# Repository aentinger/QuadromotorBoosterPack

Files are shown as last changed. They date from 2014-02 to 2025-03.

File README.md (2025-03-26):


💾 Quadromotor BoosterPack
==========================



# 📸 Image

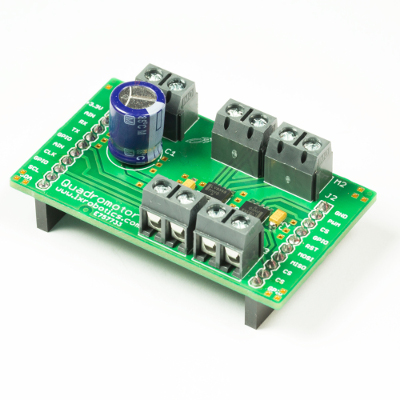
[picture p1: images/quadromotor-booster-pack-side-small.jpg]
LXRobotics P7 Quadromotor BoosterPack


# 📂 Description

The Quadromotor BoosterPack in combination with a MSP430 Launchpad facilitates the control of a 1, 2 or 4 DC motors, or alternatively  of 2 stepper motors. Additionally, outputs of the motor drivers can be connected in parallel. Therefor, two motors with an maximum output current of 2 A can be controlled, or one motor with an maximum output current of 4 A. For a quick and easy start a sample Code Composer Studio project (written in programming language C) is available.

**Features**

* Control of 1, 2 or 4 DC motors OR 
* Control of 2 stepper motors
* Speed and rotational direction adjustable
* Supply voltage range: 4 V to 16 V
* Output current per motor for 4/2/1 motors: 1 A / 2 A / 4 A
* To be used with MSP430 Launchpad
* Sample projects available for Code Composer Studio

# 🎥 [Video](images/quadromotor_booster_pack_demo.mp4)

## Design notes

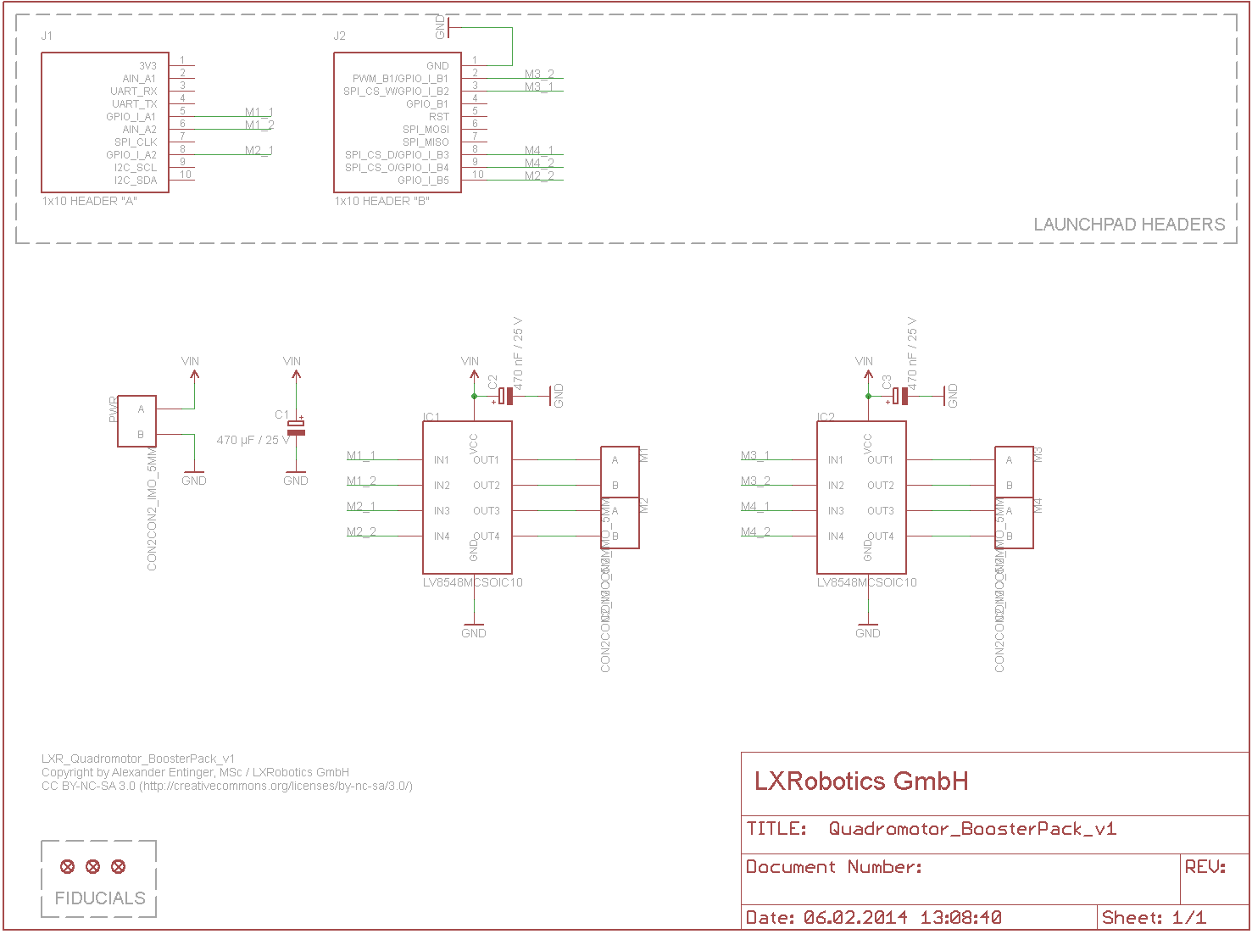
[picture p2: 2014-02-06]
hardware/lxr_quadromotor_boosterpack_v1.png

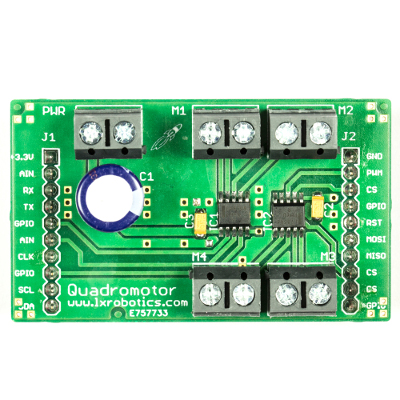
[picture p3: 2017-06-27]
images/quadromotor-booster-pack-top-small.jpg

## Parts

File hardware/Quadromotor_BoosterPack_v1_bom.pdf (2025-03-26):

Menge | Schaltplan | Bezeichnung | Farnell/Conrad Bestell Nummer | Preis (1 Stück) | Gesamtpreis | Wird bestückt | Footprint | Säckchen
2 | IC1, IC2 | LV8548MC-Motortreiber 2 CH | 2217011 | € 2,78 | € 5,56 | x
5 | PWR, M1, M2, M3, M4 | CON2, 5 mm, schwarz | 9632972 | € 0,42 | € 2,10 | | | S1
1 | C1 | 470 µF, 25 V, Elko, Radial | 1848502 | € 0,37 | € 0,37 | | | S1
2 | C2, C3 | KEMET Bauform A, 25 V, 470 nF, Tantal Ko | 1457425 | € 0,28 | € 0,56 | x
2 | J1, J2 | Pin-Header, 10-Polig, 2.54 mm | 1593464 | € 1,52 | € 3,04 | | | S1
Summe | € | 11,63

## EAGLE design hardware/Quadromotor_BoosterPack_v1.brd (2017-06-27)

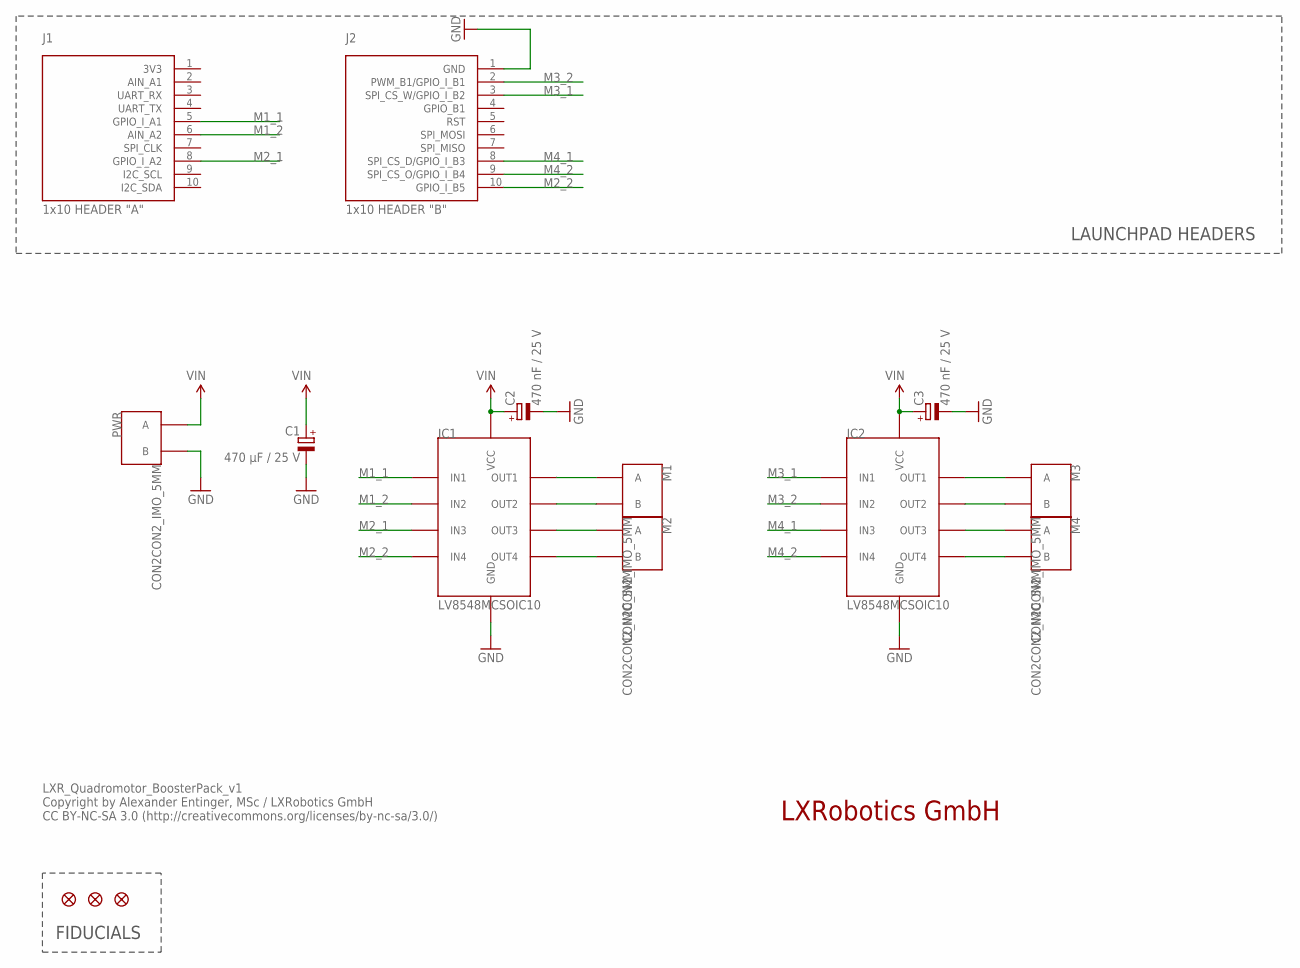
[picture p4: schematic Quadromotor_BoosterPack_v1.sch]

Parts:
C1: 470 µF / 25 V; E5-10,5
C2, C3: 470 nF / 25 V; KEMET_A
FID1, FID2, FID3: FIDUCIAL; FIDUCIAL_L10
IC1, IC2: LV8548MCSOIC10; SOIC10
J1: 1x10 HEADER "A"; 1X10
J2: 1x10 HEADER "B"; 1X10
M1, M2, M3, M4: CON2CON2_IMO_5MM; CON2_IMO
PWR: CON2CON2_IMO_5MM; CON2_IMO

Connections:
GND: C1.-, C2.CATHODE (-), C3.CATHODE (-), IC1.6 (GND), IC2.6 (GND), J2.1 (GND), PWR.P$2 (B)
M1_1: IC1.2 (IN1), J1.5 (GPIO_I_A1)
M1_2: IC1.3 (IN2), J1.6 (AIN_A2)
M2_1: IC1.4 (IN3), J1.8 (GPIO_I_A2)
M2_2: IC1.5 (IN4), J2.10 (GPIO_I_B5)
M3_1: IC2.2 (IN1), J2.3 (SPI_CS_W/GPIO_I_B2)
M3_2: IC2.3 (IN2), J2.2 (PWM_B1/GPIO_I_B1)
M4_1: IC2.4 (IN3), J2.8 (SPI_CS_D/GPIO_I_B3)
M4_2: IC2.5 (IN4), J2.9 (SPI_CS_O/GPIO_I_B4)
unnamed: IC1.10 (OUT1), M1.P$1 (A)
unnamed: IC1.9 (OUT2), M1.P$2 (B)
unnamed: IC1.8 (OUT3), M2.P$1 (A)
unnamed: IC1.7 (OUT4), M2.P$2 (B)
unnamed: IC2.10 (OUT1), M3.P$1 (A)
unnamed: IC2.9 (OUT2), M3.P$2 (B)
unnamed: IC2.8 (OUT3), M4.P$1 (A)
unnamed: IC2.7 (OUT4), M4.P$2 (B)
VIN: C1.+, C2.ANODE (+), C3.ANODE (+), IC1.1 (VCC), IC2.1 (VCC), PWR.P$1 (A)

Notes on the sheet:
LAUNCHPAD HEADERS
FIDUCIALS
LXRobotics GmbH
LXR_Quadromotor_BoosterPack_v1 Copyright by Alexander Entinger, MSc / LXRobotics GmbH CC BY-NC-SA 3.0 (http://creativecommons.org/licenses/by-nc-sa/3.0/)

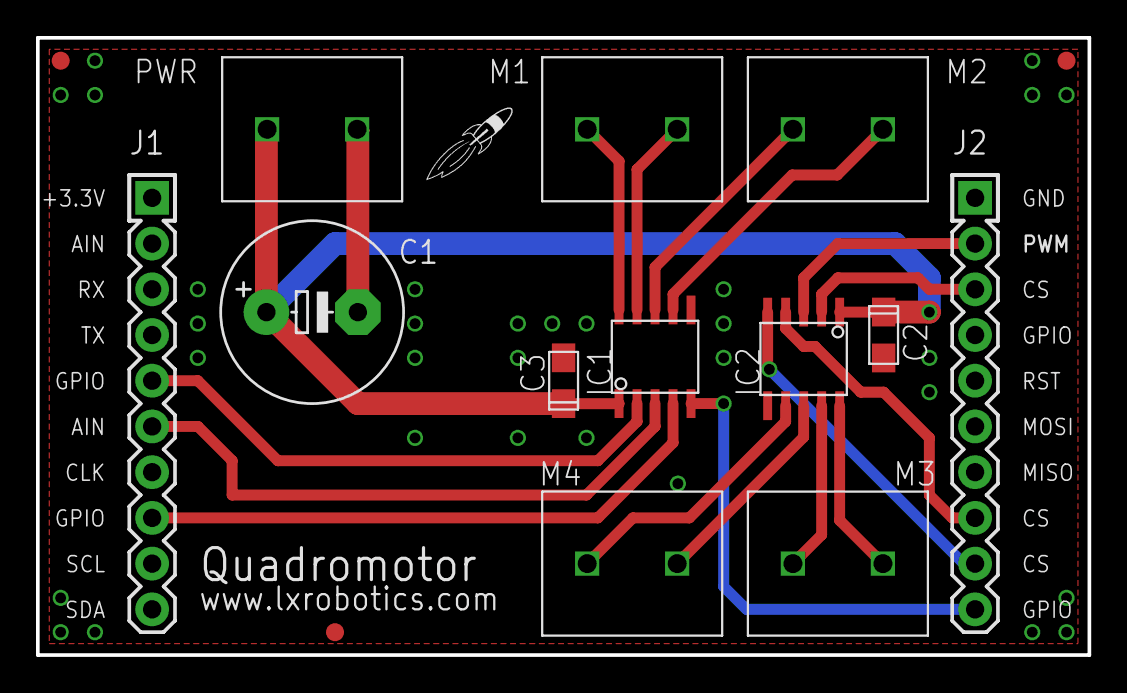
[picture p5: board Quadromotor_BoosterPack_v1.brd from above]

Board: 2 copper layers, 58.4 x 34.3 mm, 16 parts (0 on the bottom side), 18 nets.

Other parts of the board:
U$1: LOGO-ROCKET

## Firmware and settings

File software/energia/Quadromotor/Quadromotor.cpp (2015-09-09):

/**
 * @author Alexander Entinger, MSc
 * @brief energia library file for the LXRobotics Quadromotor Booster Pack ( https://www.lxrobotics.com/produkte/booster-packs/quadromotor-boosterpack )
 * @file Quadromotor.h
 * @license CC BY-NC-SA 3.0 ( http://creativecommons.org/licenses/by-nc-sa/3.0/ )
 */
 
/* INCLUDES */

#include "Quadromotor.h"

/* FUNCTIONS */

/* C */

#include <msp430.h>

/* DEFINES */
#define M1_1_DIR		(P1DIR)
#define M1_2_DIR		(P1DIR)
#define M1_1_OUT		(P1OUT)
#define M1_2_OUT		(P1OUT)
#define M1_1			(1<<3)
#define M1_2			(1<<4)

#define M2_1_DIR		(P2DIR)
#define M2_2_DIR		(P2DIR)
#define M2_1_OUT		(P2OUT)
#define M2_2_OUT		(P2OUT)
#define M2_1			(1<<0)
#define M2_2			(1<<3)

#define M3_1_DIR		(P2DIR)
#define M3_2_DIR		(P2DIR)
#define M3_1_OUT		(P2OUT)
#define M3_2_OUT		(P2OUT)
#define M3_1			(1<<7)
#define M3_2			(1<<6)

#define M4_1_DIR		(P2DIR)
#define M4_2_DIR		(P2DIR)
#define M4_1_OUT		(P2OUT)
#define M4_2_OUT		(P2OUT)
#define M4_1			(1<<5)
#define M4_2			(1<<4)

/* MACROS */
#define M1_1_HIGH		M1_1_OUT |= M1_1
#define M1_1_LOW		M1_1_OUT &= ~M1_1
#define M1_2_HIGH		M1_2_OUT |= M1_2
#define M1_2_LOW		M1_2_OUT &= ~M1_2

#define M2_1_HIGH		M2_1_OUT |= M2_1
#define M2_1_LOW		M2_1_OUT &= ~M2_1
#define M2_2_HIGH		M2_2_OUT |= M2_2
#define M2_2_LOW		M2_2_OUT &= ~M2_2

#define M3_1_HIGH		M3_1_OUT |= M3_1
#define M3_1_LOW		M3_1_OUT &= ~M3_1
#define M3_2_HIGH		M3_2_OUT |= M3_2
#define M3_2_LOW		M3_2_OUT &= ~M3_2

#define M4_1_HIGH		M4_1_OUT |= M4_1
#define M4_1_LOW		M4_1_OUT &= ~M4_1
#define M4_2_HIGH		M4_2_OUT |= M4_2
#define M4_2_LOW		M4_2_OUT &= ~M4_2

/* DATA TYPES */

typedef struct {
	uint16_t speed;
	E_DIRECTION dir;
} s_motor_params;

/* GLOBAL VARIABLES */

static volatile s_motor_params m_motor_1 = {0, FWD};
static volatile s_motor_params m_motor_2 = {0, FWD};
static volatile s_motor_params m_motor_3 = {0, FWD};
static volatile s_motor_params m_motor_4 = {0, FWD};

/* GLOBAL FUNCTIONS */

/**
 * @brief initializes the booster pack
 */
void init_quadromotor_booster_pack()  {
	// set all gpios to outputs and low
	M1_1_DIR |= M1_1;	M1_1_LOW;
	M1_2_DIR |= M1_2;	M1_2_LOW;
	M2_1_DIR |= M2_1;	M2_1_LOW;
	M2_2_DIR |= M2_2;	M2_2_LOW;
	M3_1_DIR |= M3_1;	M3_1_LOW;
	M3_2_DIR |= M3_2;	M3_2_LOW;
	M4_1_DIR |= M4_1;	M4_1_LOW;
	M4_2_DIR |= M4_2;	M4_2_LOW;

	// disable all secondary port functions
	P1SEL = 0x00; P1SEL2 = 0x00;
	P2SEL = 0x00; P2SEL2 = 0x00;

	TA0CTL |= TASSEL_2;	// select SMCLK as clock source, thats 16 MHz, divider = 8, 1 timerstep = 500 ns
	TA0CTL |= 0xC0;
	TA0CTL |= TACLR;		// clear the timer

	TA0CCR0 = 2016;		// equals 1 ms
	TA0CCTL0 &= CCIFG;
	TA0CCTL0 |= CCIE;		// enable capture compare interrupt

	TA0CTL &= ~TAIFG;	// clear the inerrupt flag
	TA0CTL |= TAIE;		// enable the interrupt
	TA0CTL |= MC_1;		// timer counts up to TACCR0

	TA0CCR1 = 0x0000;
	TA0CCTL1 &= CCIFG;
	TA0CCTL1 |= CCIE;		// enable capture compare interrupt

	TA0CCR2 = 0x0000;
	TA0CCTL2 &= CCIFG;
	TA0CCTL2 |= CCIE;		// enable capture compare interrupt

	TA1CTL |= TASSEL_2;	// select SMCLK as clock source, thats 16 MHz, divider = 8, 1 timerstep = 500 ns
	TA1CTL |= 0xC0;
	TA1CTL |= TACLR;		// clear the timer

	TA1CCR0 = 2016;		// equals 1 ms
	TA1CCTL0 &= CCIFG;
	TA1CCTL0 |= CCIE;		// enable capture compare interrupt

	TA1CTL &= ~TAIFG;	// clear the inerrupt flag
	TA1CTL |= TAIE;		// enable the interrupt
	TA1CTL |= MC_1;		// timer counts up to TACCR0

	TA1CCR1 = 0x0000;
	TA1CCTL1 &= CCIFG;
	TA1CCTL1 |= CCIE;		// enable capture compare interrupt
	TA1CCR2 = 0x0000;
	TA1CCTL2 &= CCIFG;
	TA1CCTL2 |= CCIE;		// enable capture compare interrupt
}

/**
 * @brief set speed for motor 1
 * @param speed 0 means no speak and 1000 means full speed
 */
void motor_1_set_speed(uint16_t const speed) {
	noInterrupts();
	if(speed <= MAX_SPEED) {
		m_motor_1.speed = (speed<<1); // multiply with 2
	}
	interrupts();
}

/**
 * @brief set direction for motor 1
 */
void motor_1_set_direction(E_DIRECTION const dir) {
	noInterrupts();
	m_motor_1.dir = dir;
	interrupts();
}

/**
 * @brief set speed for motor 2
 * @param speed 0 means no speak and 1000 means full speed
 */
void motor_2_set_speed(uint16_t const speed) {
	noInterrupts();
	if(speed <= MAX_SPEED) {
		m_motor_2.speed = (speed<<1); // multiply with 2
	}
	interrupts();
}

/**
 * @brief set direction for motor 2
 */
void motor_2_set_direction(E_DIRECTION const dir) {
	noInterrupts();
	m_motor_2.dir = dir;
	interrupts();
}

/**
 * @brief set speed for motor 3
 * @param speed 0 means no speak and 1000 means full speed
 */
void motor_3_set_speed(uint16_t const speed) {
	noInterrupts();
	if(speed <= MAX_SPEED) {
		m_motor_3.speed = (speed<<1); // multiply with 2
	}
	interrupts();
}

/**
 * @brief set direction for motor 3
 */
void motor_3_set_direction(E_DIRECTION const dir) {
	noInterrupts();
	m_motor_3.dir = dir;
	interrupts();
}

/**
 * @brief set speed for motor 4
 * @param speed 0 means no speak and 1000 means full speed
 */
void motor_4_set_speed(uint16_t const speed) {
	noInterrupts();
	if(speed <= MAX_SPEED) {
		m_motor_4.speed = (speed<<1); // multiply with 2
	}
	interrupts();
}

/**
 * @brief set direction for motor 4
 */
void motor_4_set_direction(E_DIRECTION const dir) {
	noInterrupts();
	m_motor_4.dir = dir;
	interrupts();
}

/**
 * @brief Timer A0 Interrupt Service Routine for CCR0
 */
#pragma vector=TIMER0_A0_VECTOR
__interrupt void TIMER0_A0_ISR(void) {
	// update the capture compare registers
	TA0CCR1 = m_motor_1.speed;
	TA0CCR2 = m_motor_2.speed;
	// set the pins
	if(m_motor_1.speed > 0) {
		if(m_motor_1.dir == FWD) {
			M1_1_HIGH; M1_2_LOW;
		} else if(m_motor_1.dir == BWD) {
			M1_1_LOW; M1_2_HIGH;
		}
	} else {
		M1_1_LOW; M1_2_LOW;
	}
	if(m_motor_2.speed > 0) {
		if(m_motor_2.dir == FWD) {
			M2_1_HIGH; M2_2_LOW;
		} else if(m_motor_2.dir == BWD) {
			M2_1_LOW; M2_2_HIGH;
		}
	} else {
		M2_1_LOW; M2_2_LOW;
	}
}

/**
 * @brief Timer A0 Interrupt Service Routine for all the other interrupts
 */
#pragma vector=TIMER0_A1_VECTOR
__interrupt void TIMER0_A1_ISR(void) {

	switch (TA0IV) {
	case 0: break; // no interrupt
	case 2: {
		M1_1_LOW; M1_2_LOW;
	}
		break;
	case 4: {
		M2_1_LOW; M2_2_LOW;
	}
		break;
	case 6:	break; // reserved
	case 8:	break; // reserved
	case 10: break; // overflow
	default: break;
	}
}

/**
 * @brief Timer A1 Interrupt Service Routine for CCR0
 */
#pragma vector=TIMER1_A0_VECTOR
__interrupt void TIMER1_A0_ISR(void) {
	// update the capture compare registers
	TA1CCR1 = m_motor_3.speed;
	TA1CCR2 = m_motor_4.speed;
	// set the pins
	if(m_motor_3.speed > 0) {
		if(m_motor_3.dir == FWD) {
			M3_1_HIGH; M3_2_LOW;
		} else if(m_motor_3.dir == BWD) {
			M3_1_LOW; M3_2_HIGH;
		}
	} else {
		M3_1_LOW; M3_2_LOW;
	}
	if(m_motor_4.speed > 0) {
		if(m_motor_4.dir == FWD) {
			M4_1_HIGH; M4_2_LOW;
		} else if(m_motor_4.dir == BWD) {
			M4_1_LOW; M4_2_HIGH;
		}
	} else {
		M4_1_LOW; M4_2_LOW;
	}
}
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

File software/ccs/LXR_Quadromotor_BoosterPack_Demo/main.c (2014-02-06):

/**
 * @author Alexander Entinger, MSc / LXRobotics GmbH
 * @brief demo file how to use the quadromotor booster pack
 * @file main.c
 * @license CC BY-NC-SA 3.0 ( http://creativecommons.org/licenses/by-nc-sa/3.0/ )
 */

#include <msp430.h> 

#include "LXR_Quadromotor_BoosterPack.h"

/* PROTOTYPE SECTION */
void setup_clock();
void test_four_single_motors();
void test_two_dual_motors();
void test_single_motor();

/* PROGRAM SECTION */

int main(void) {
    WDTCTL = WDTPW | WDTHOLD;	// Stop watchdog timer

    setup_clock();

    init_quadromotor_booster_pack();

    test_four_single_motors();
    //test_two_dual_motors();
    //test_single_motor();

    for(;;) {
    	// loop forever, dont return
    	asm(" NOP ");
    }
}

/**
 * @brief setup the clock so the internal dco generates 16 MHz
 */
void setup_clock() {
	  if (CALBC1_16MHZ==0xFF) {					// If calibration constants erased
	    for(;;) asm(" NOP ");                    // do not load, trap CPU!!
	  }
	  DCOCTL = 0;                               // Select lowest DCOx and MODx settings
	  BCSCTL1 = CALBC1_16MHZ;                   // Set range
	  DCOCTL = CALDCO_16MHZ;                    // Set DCO step + modulation*/
}

/**
 * @brief use the booster pack to control 4 different motors independently from one another
 */
void test_four_single_motors() {
	motor_1_set_direction(FWD);
	motor_1_set_speed(250);

	motor_2_set_direction(BWD);
	motor_2_set_speed(500);

	motor_3_set_direction(FWD);
	motor_3_set_speed(750);

	motor_4_set_direction(BWD);
	motor_4_set_speed(1000);
}

/**
 * @brief use the booster pack to control 2 different motors independently from one another, but with double strength
 */
void test_two_dual_motors() {
	motor_1_set_direction(FWD);
	motor_1_set_speed(250);

	motor_2_set_direction(BWD);
	motor_2_set_speed(750);
}

/**
 * @brief use the booster pack to control 1 but with four times the strength of one single motor
 */
void test_single_motor() {
	motor_1_set_direction(FWD);
	motor_1_set_speed(500);
}

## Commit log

2014-02-09 added stepper demo software
2017-06-27 Adding hardware + images
    [Quadromotor_BoosterPack_v1.brd, Quadromotor_BoosterPack_v1.sch]
2025-03-26 Upload BOM.

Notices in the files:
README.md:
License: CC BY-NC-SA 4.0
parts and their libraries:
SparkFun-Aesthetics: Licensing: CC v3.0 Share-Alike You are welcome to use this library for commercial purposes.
